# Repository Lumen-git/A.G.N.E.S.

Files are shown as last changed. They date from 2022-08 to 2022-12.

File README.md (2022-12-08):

# A.G.N.E.S.
### Automated Garden & Nurturing Environment System 
<br>

## Meet A.G.N.E.S.
I'll answer the biggest question first. Why Agnes? This was very much a case of I wanted a cool name for this thing, then came up with the acronym later. Also, as one may be able to tell, heavily inspired by GLaDOS, which could be a good or a bad thing depending on your opinion on evil omnipresent AIs.

Agnes was designed with the intent of automating a small herb box, flower pot, or with upgrades that can be easily added with some quick fixes to the code and a better central processor, a small garden or greenhouse. The two main focuses of Agnes are water and light. Light is easy, just turning on and off according to an internal timer. Watering is done every 12th hour of every day. Every 5 minutes during the 12th hour, the soil moisture is checked. If the moisture level is low, a pump is turned on to send water through a tube and onto the soil. A DHT is also added to monitor the surrounding air temperature and humidity. This information isn't used to judge lighting or water, but is displayed to the user on a screen to show environmental details, as well as soil moisture and system time.

## The Wiring
The wiring can be seen in the Fritzing file below, as well as the .fzz file and PDF in the repo. The red and blue wires represent 5V and ground, and the other colored wires are basic I/O and data wires. The black wires coming off the relays splice into the 120V supply of the lamp and water pump. It is highly recommended to use capacitive soil moisture sensors over traditional bare metal sensors as they last much longer. 

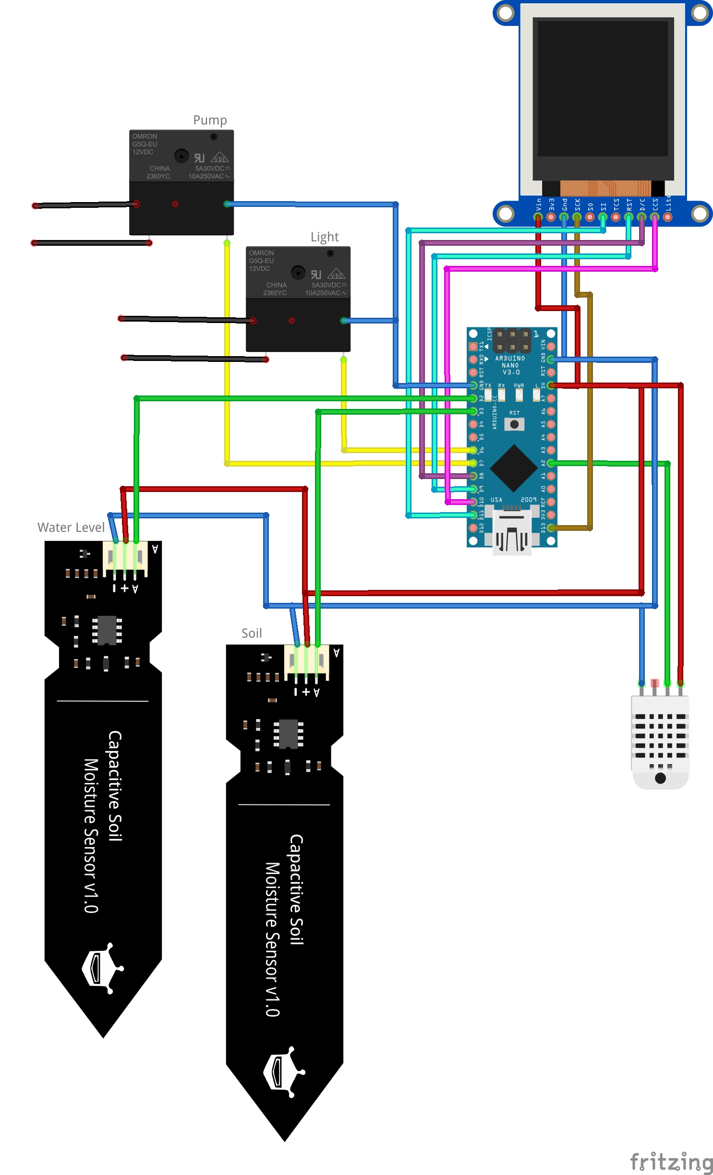
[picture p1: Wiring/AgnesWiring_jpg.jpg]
Wires


Here it is worth noting that I do not consider myself an electrical engineer, not even as a hobbyist. While I have built this and there were no fires, I cannot at all guarantee that controlling mains voltage or having this many 5V and ground connections on an Arduino nano is safe. If I had one spare, I may have preferred an Arduino Uno. I also did a considerable amount of searching online, but wasn't able to find a better solution for controlling the lamp and pump than 2 120V relays. I would love to not have to deal with cutting and tapping into the 120V cables, but for now it seems to work. These are 2 improvements I hope to make on Agnes V2.

## Important Physical Design  
### The water reservoir
I constructed my water reservoir by submerging a small fish tank pump into a 5 gallon bucket and running a 1 inch flexible PVC tube up to the plant. About 2 inches above the top of the pump I cut a slit to slide the water detecting sensor in and sealed it with silicon putty. This sensor will return a low value when the water level dips too low and displays a message to the screen. 

### The water tube
The water tube was a 1 inch flexible PVC tube running from the water bucket up to the plants. It was mounted just above the soil and had many small holes drilled in it to let the water out. The pump on time may need to be adjusted the code based on your water delivery method.

### The brains box
The Arduino was encased in a waterproof project box mounted to the side of the plant box. Holes were drilled to allow all the sensor wires in as well as the 120V wires to the relays that were also housed inside. A hole was cut in the front to allow the screen to fit.

## Flaws and To-Do

The biggest 2 are make sure the power supply of the Arduino isn't being overloaded and find a better way to control the mains voltage. 

Understanding electrical engineering would also be a good start.

For version 2, I intend on using a WiFi enabled microcontroller to allow the user to monitor stats on a local website, as well as see watering and soil moisture history. This would also allow for a more refined way for the user to set variables. 

## Final notes

Working on A.G.N.E.S. during college and having to juggle lack of time, materials, and space, its far rom perfect. Hopefully this is a good jumping off point for version 2 which will more closely resemble a more formal project. Until then, all the code and designs are open source and ready for builds and improvements!

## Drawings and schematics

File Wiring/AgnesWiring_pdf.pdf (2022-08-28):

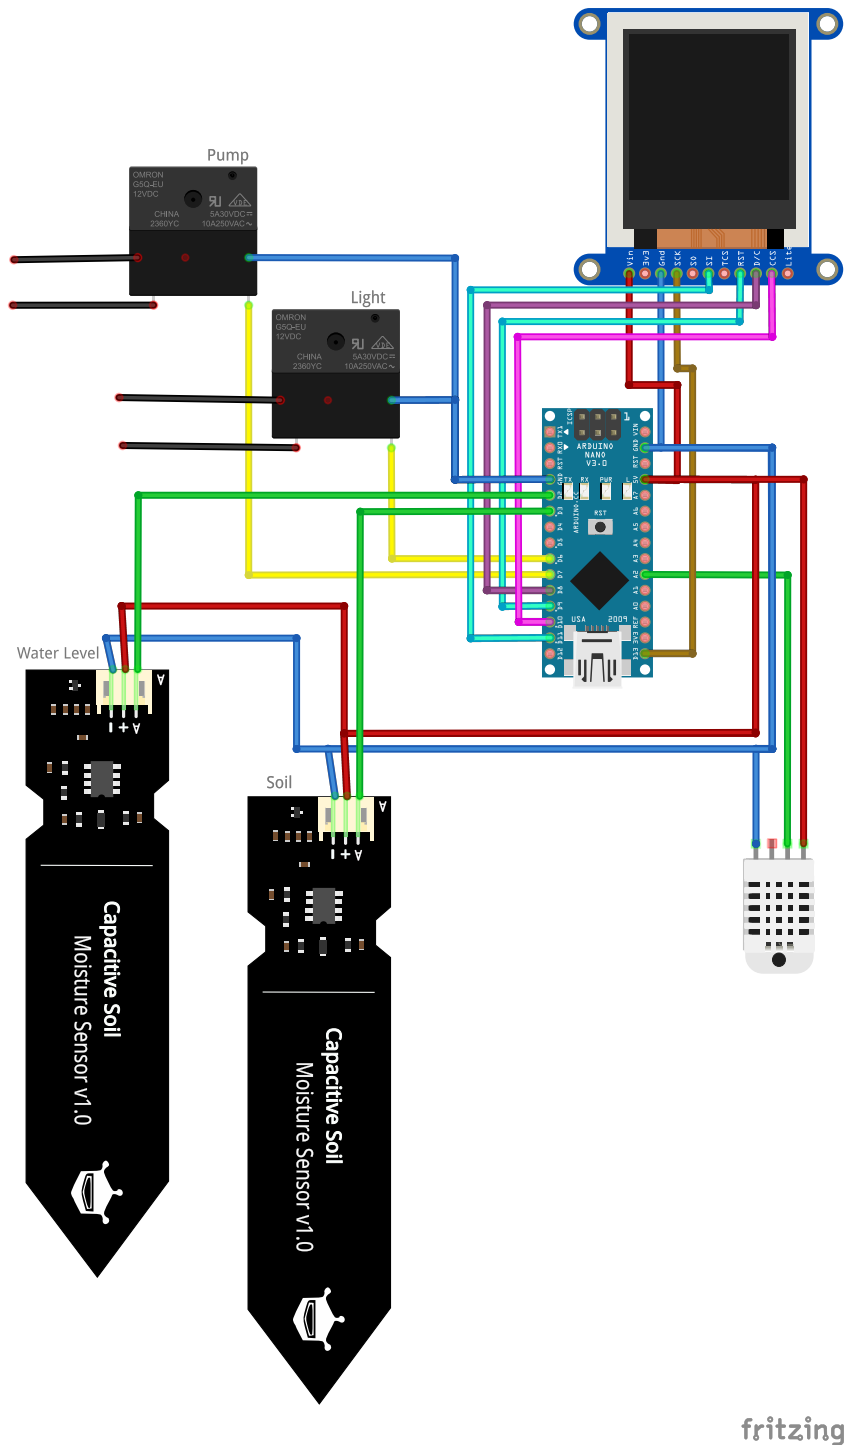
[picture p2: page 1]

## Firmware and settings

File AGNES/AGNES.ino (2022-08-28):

//AGNES
//Lumen

String aVersion = "1.0.2";

//Include Statements

#include <DHT.h>
#include <DHT_U.h>
#include <Adafruit_GFX.h>
#include <Adafruit_ST7735.h>
#include <Adafruit_ST7789.h>
#include <SPI.h>
#include <Time.h>
#include <TimeLib.h>

int WaterLevel = 2; //Water level sensor
int SoilMoisture = 3; //Soil moisture sensor
int TempHumidity = 2; //Environment Sensor
int PumpRelay = 7; //Relay to control pump
int LightRelay = 6; //Relay to control lights

//LCD Pins
int LCDclk = 13; //LCD CLK pin
int LCDmosi = 11; //LCD MOSI pin
int LCDrst = 9; //LCD RST pin
int LCDcs = 10; //LCD CS pin
int LCDdc = 8; // LCD DIC pin

//Set up DHT sensor
//Analog 2
DHT dht(2, DHT22);

//Set up LCD
Adafruit_ST7735 tft = Adafruit_ST7735(LCDcs, LCDdc, LCDrst);

// 'AgnesSpashScreen', 148x36px
const unsigned char epd_bitmap_AgnesSpashScreen [] PROGMEM = {
  0x00, 0x7f, 0x80, 0x07, 0xf8, 0x00, 0x00, 0x00, 0x00, 0x00, 0x00, 0x00, 0x00, 0x00, 0x00, 0x00, 
  0x00, 0x00, 0x00, 0x00, 0x7f, 0x80, 0x07, 0xf8, 0x00, 0x00, 0x00, 0x00, 0x00, 0x00, 0x00, 0x00, 
  0x00, 0x00, 0x00, 0x00, 0x00, 0x00, 0x00, 0x7f, 0x80, 0x07, 0xf8, 0x00, 0x00, 0x00, 0x00, 0x00, 
  0x00, 0x00, 0x00, 0x00, 0x00, 0x00, 0x00, 0x00, 0x00, 0x00, 0x7f, 0x80, 0x07, 0xf8, 0x00, 0x00, 
  0x00, 0x00, 0x00, 0x00, 0x00, 0x00, 0x00, 0x00, 0x00, 0x00, 0x00, 0x00, 0x07, 0x80, 0x78, 0x78, 
  0x07, 0x80, 0x00, 0x00, 0x00, 0x00, 0x00, 0x00, 0x00, 0x00, 0x00, 0x00, 0x00, 0x00, 0x00, 0x07, 
  0x80, 0x78, 0x78, 0x07, 0x80, 0x00, 0x00, 0x00, 0x00, 0x00, 0x00, 0x00, 0x00, 0x00, 0x00, 0x00, 
  0x00, 0x00, 0x07, 0x80, 0x78, 0x78, 0x07, 0x80, 0x00, 0x00, 0x00, 0x00, 0x00, 0x00, 0x00, 0x00, 
  0x00, 0x00, 0x00, 0x00, 0x00, 0x07, 0x80, 0x78, 0x78, 0x07, 0x80, 0x00, 0x30, 0x00, 0x07, 0xc0, 
  0x0c, 0x00, 0xc0, 0xff, 0xfc, 0x00, 0x7c, 0x00, 0x07, 0x87, 0xf8, 0x7f, 0x87, 0x80, 0x00, 0x38, 
  0x00, 0x1f, 0xf0, 0x1e, 0x00, 0xe0, 0xff, 0xfc, 0x01, 0xff, 0x00, 0x07, 0x87, 0xf8, 0x7f, 0x87, 
  0x80, 0x00, 0x78, 0x00, 0x7e, 0xf8, 0x1e, 0x00, 0xe0, 0xff, 0xfc, 0x07, 0xef, 0x80, 0x07, 0x87, 
  0xf8, 0x7f, 0x87, 0x80, 0x00, 0x78, 0x00, 0x70, 0x3c, 0x1f, 0x00, 0xe0, 0xe0, 0x00, 0x07, 0x03, 
  0xc0, 0x07, 0x87, 0xf8, 0x7f, 0x87, 0x80, 0x00, 0x7c, 0x00, 0xe0, 0x1c, 0x1f, 0x00, 0xe0, 0xe0, 
  0x00, 0x0e, 0x01, 0xe0, 0x7f, 0x80, 0x00, 0x00, 0x07, 0xf8, 0x00, 0xfc, 0x00, 0xe0, 0x0e, 0x1f, 
  0x80, 0xe0, 0xe0, 0x00, 0x0e, 0x00, 0xe0, 0x7f, 0x80, 0x00, 0x00, 0x07, 0xf8, 0x00, 0xec, 0x01, 
  0xc0, 0x0e, 0x1f, 0x80, 0xe0, 0xe0, 0x00, 0x0e, 0x00, 0xe0, 0x7f, 0x80, 0x00, 0x00, 0x07, 0xf8, 
  0x00, 0xce, 0x01, 0xc0, 0x00, 0x1d, 0xc0, 0xe0, 0xe0, 0x00, 0x0e, 0x00, 0x00, 0x7f, 0x80, 0x00, 
  0x00, 0x07, 0xf8, 0x01, 0xce, 0x01, 0xc0, 0x00, 0x1c, 0xe0, 0xe0, 0xe0, 0x00, 0x0f, 0x00, 0x00, 
  0x00, 0x78, 0x78, 0x78, 0x78, 0x00, 0x01, 0xc6, 0x01, 0xc0, 0x00, 0x1c, 0xe0, 0xe0, 0xe0, 0x00, 
  0x07, 0x80, 0x00, 0x00, 0x78, 0x78, 0x78, 0x78, 0x00, 0x01, 0x87, 0x01, 0xc0, 0x00, 0x1c, 0x70, 
  0xe0, 0xe0, 0x00, 0x07, 0xe0, 0x00, 0x00, 0x78, 0x78, 0x78, 0x78, 0x00, 0x03, 0x87, 0x01, 0xc0, 
  0x00, 0x1c, 0x70, 0xe0, 0xff, 0xf8, 0x01, 0xfc, 0x00, 0x00, 0x78, 0x78, 0x78, 0x78, 0x00, 0x03, 
  0x83, 0x01, 0xc0, 0xfe, 0x1c, 0x38, 0xe0, 0xff, 0xf8, 0x00, 0x7f, 0x00, 0x7f, 0x80, 0x00, 0x00, 
  0x07, 0xf8, 0x03, 0x03, 0x81, 0xc0, 0xfe, 0x1c, 0x38, 0xe0, 0xe0, 0x00, 0x00, 0x1f, 0x80, 0x7f, 
  0x80, 0x00, 0x00, 0x07, 0xf8, 0x07, 0x03, 0x81, 0xc0, 0xfe, 0x1c, 0x1c, 0xe0, 0xe0, 0x00, 0x00, 
  0x03, 0xc0, 0x7f, 0x80, 0x00, 0x00, 0x07, 0xf8, 0x07, 0xff, 0x81, 0xc0, 0x0e, 0x1c, 0x1c, 0xe0, 
  0xe0, 0x00, 0x00, 0x01, 0xe0, 0x7f, 0x80, 0x00, 0x00, 0x07, 0xf8, 0x07, 0xff, 0x81, 0xc0, 0x0e, 
  0x1c, 0x0e, 0xe0, 0xe0, 0x00, 0x00, 0x00, 0xe0, 0x07, 0x87, 0xf8, 0x7f, 0x87, 0x80, 0x0f, 0xff, 
  0xc1, 0xc0, 0x0e, 0x1c, 0x0f, 0xe0, 0xe0, 0x00, 0x1c, 0x00, 0xe0, 0x07, 0x87, 0xf8, 0x7f, 0x87, 
  0x80, 0x0e, 0x01, 0xc0, 0xe0, 0x0e, 0x1c, 0x07, 0xe0, 0xe0, 0x00, 0x1c, 0x00, 0xe0, 0x07, 0x87, 
  0xf8, 0x7f, 0x87, 0x80, 0x0e, 0x00, 0xc0, 0xe0, 0x0e, 0x1c, 0x07, 0xe0, 0xe0, 0x00, 0x1e, 0x00, 
  0xe0, 0x07, 0x87, 0xf8, 0x7f, 0x87, 0x80, 0x0c, 0x00, 0xe0, 0x70, 0x0e, 0x1c, 0x03, 0xe0, 0xe0, 
  0x00, 0x0f, 0x01, 0xe0, 0x07, 0x80, 0x78, 0x78, 0x07, 0x80, 0x1c, 0x00, 0xe0, 0x7c, 0x3e, 0x1c, 
  0x03, 0xe0, 0xe0, 0x00, 0x07, 0x83, 0xc0, 0x07, 0x80, 0x78, 0x78, 0x07, 0x80, 0x1c, 0x00, 0x60, 
  0x3f, 0xf8, 0x1c, 0x01, 0xe0, 0xff, 0xfc, 0x03, 0xff, 0x80, 0x07, 0x80, 0x78, 0x78, 0x07, 0x80, 
  0x18, 0x00, 0x70, 0x0f, 0xf0, 0x1c, 0x01, 0xe0, 0xff, 0xfc, 0x00, 0xfe, 0x00, 0x07, 0x80, 0x78, 
  0x78, 0x07, 0x80, 0x00, 0x00, 0x00, 0x00, 0x00, 0x00, 0x00, 0x00, 0x00, 0x00, 0x00, 0x00, 0x00, 
  0x00, 0x7f, 0x80, 0x07, 0xf8, 0x00, 0x00, 0x00, 0x00, 0x00, 0x00, 0x00, 0x00, 0x00, 0x00, 0x00, 
  0x00, 0x00, 0x00, 0x00, 0x7f, 0x80, 0x07, 0xf8, 0x00, 0x00, 0x00, 0x00, 0x00, 0x00, 0x00, 0x00, 
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
};

void splash(){
    tft.fillScreen(ST77XX_BLACK);
    tft.setTextColor(ST77XX_WHITE);
    tft.setTextSize(1);
    tft.drawBitmap(1, 46, epd_bitmap_AgnesSpashScreen, 148, 36, ST77XX_WHITE);
    tft.setCursor(110, 85);
    tft.print("V. ");
    tft.println(aVersion);
}

void setup() {
  
  Serial.begin(9600);

  //Start LCD and show splashscreen
  tft.initR(INITR_BLACKTAB); 
  tft.setRotation(3);
  splash();

  pinMode(LightRelay, OUTPUT);
  pinMode(PumpRelay, OUTPUT);
  pinMode(LCDclk, OUTPUT);
  pinMode(LCDmosi, OUTPUT);
  pinMode(LCDrst, OUTPUT);
  pinMode(LCDcs, OUTPUT);
  pinMode(LCDdc, OUTPUT);

  Serial.println("Pin Modes Set");

  dht.begin();

  Serial.println("DHT loaded");

  Serial.print("Welcome to A.G.N.E.S. Version ");
  Serial.println(aVersion);

  delay(1000);
  tft.fillScreen(ST77XX_BLACK);
}

//CONTROL VARIABLES
//TIME (In microseconds, seconds x 1000)
long wait = 60000L;
int water = 3000;
//TIME (In hours)
int lightHours = 15; //Desired hours - 1 (i.e. enter 15 for 16 hours of light)
//SOIL MOISTURE
int moisturePercent = 15; //Level of moisture tha triggers watering
//MOISTURE CALIBRATION
//Soil should be pretty accurate, water just needs to be good enough
int soilDry = 833;
int soilWet = 823;
int waterDry = 282;
int waterWet = 203;


void loop() {

  //DO EVERYTHING BELOW ON EVERY LOOP
  //Read from sensors
  float soilMoisture = analogRead(SoilMoisture);
  float waterLevel = analogRead(WaterLevel);
  float temperature = dht.readTemperature(true);
  float humidity = dht.readHumidity();

  //Convert moisture readings to % and water status
  float percentSoil = map(soilMoisture, soilWet, soilDry, 100, 0);
  float percentWater = map(waterLevel, waterWet, waterDry, 100, 0);
  bool waterFull = percentWater > 50;

  //Check the current hour (since boot)
  int isHour = hour();
  int isMinute = minute();
  

  //PRINT EVERYTHING TO SERIAL
  Serial.println("-----------------------------");
  Serial.print("System time is " );
  Serial.print(isHour);
  Serial.print(":");
  Serial.println(isMinute);
  Serial.print("Soil moisture level:  ");
  Serial.print(percentSoil);
  Serial.println("%");
  Serial.print("Environmental temperature: ");
  Serial.print(temperature);
  Serial.println(" F");
  Serial.print("Environmental humidity is ");
  Serial.print(humidity);
  Serial.println("%");
  Serial.print("Water reservoir is ");
  if (waterFull){
    Serial.println("full");
   } else {
    Serial.println("low");
   }
  Serial.print("Current soil reading: ");
  Serial.println(soilMoisture);

   //SET SCREEN PROPERTIES
   tft.fillScreen(ST77XX_BLACK);
   tft.setTextColor(ST77XX_WHITE);
   tft.setCursor(0, 0);
   tft.setTextSize(0);

   //PRINT IMPORTANT PARTS TO SCREEN
   tft.print("Soil moisture: ");
   tft.print(percentSoil);
   tft.println("%");
   tft.print("Env. temperature: ");
   tft.print(temperature);
   tft.println(" F");
   tft.print("Env. humidity: ");
   tft.print(humidity);
   tft.println("%");

   if (!waterFull){
      tft.setTextColor(ST77XX_RED);
      tft.setTextSize(2);
      tft.setCursor(0, 90);
      tft.println("Check Water");
      tft.println("Level!!");
    }

  
  //FUNCTIONS THAT RUN AT CERTAIN TIMES/CONDITIONS
  //Turn on light from 0-lightHours hours
  if (isHour < lightHours){
    digitalWrite(LightRelay, LOW);
    tft.drawChar(155, 0, 0x2A, ST7735_WHITE, ST7735_BLACK, 1);
   } else {
    digitalWrite(LightRelay, HIGH);
   }

  //If soil is less than moisturePercent% moisture, turn on pump for water microseconds
  //Remove the pumping time from the total wait
  //Only check/water during the 12th hour
  if (isHour == 12){
   if (percentSoil < moisturePercent){
      Serial.println("Watering...");
      digitalWrite(PumpRelay, HIGH);
      delay(water);
      digitalWrite(PumpRelay, LOW);
      wait = wait - water;
    }
  }

  
  //Loop every minute
  delay(wait);


}

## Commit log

2022-08-28 Movied to file to make Arduino Happy
2022-08-28 Moved code to folder to make Arduino happy
2022-08-28 Added Fritzing file
    [AgnesWiring.fzz]
2022-08-28 Adding wiring images
2022-08-29 Moved files
    [AgnesWiring.fzz]
